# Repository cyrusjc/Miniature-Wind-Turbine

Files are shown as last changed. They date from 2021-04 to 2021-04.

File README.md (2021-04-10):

# Miniature-Wind-Turbine
ELEC 391 Design Project. Miniature Wind Turbine, hand wound generator, 3D printed turbine blades, with a buck converter for MPPT, uploaded onto a cloud server, built with lego.



fig.1 Windmill in question

For the PCB, Altium designer was used, and ordered off of an online PCB manufacturer in china. Voltmeter uses a voltage follower and Ammeter uses Shunt resistor with a differential amplifier.



fig.2 PCB with Boost Converter using 1 diode and 1 mosfet topology.

For the MPPT algo, we used P&O which is state dependent. checks previous power and duty cycle. the flow chart of the logic is listed below:



The MPPT algo is modeled on matLAB using a special function block:



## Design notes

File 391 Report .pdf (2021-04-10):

### ELEC 391 Engineering Report: Wind Tracking Power Generator

### Submitted by:

Name | Student Number
Berk Calis | 31602155
Bruno Rodriguez | 19024173
Cyrus Cheung | 77080844
Felipe Ballesteros | 10703156

### Submitted for: ELEC 391 On Apr 14th, 2019 Professors: Ignacio Galliano Zurbriggen & Cristian Grecu

Abstract

This term, for our ELEC 391, Design Studio course, we set out to design a wind turbine that will generate power from a box fan provided to us. The requirement is that for our wind turbine is that is must meet dimensional requirement of 50x50x60cm and our boost converter must produce 10V - 15V output. Our goal for this project was to create an efficient turbine made with recycled materials. We settled on using legos for our chassis, since one of our members had previously owned them. We designed our turbine to be a 3-phase PMSG. Our generator will be equipped with a MPPT algorithm that controls duty cycle of our boost converter. With our design, we managed to provide 1.4 W of power with a 100Ω load. Our turbine is able to sense the wind and rotate our generator to track our wind with a 180° arc. To complete our system, we created a website, that has four main features: real-time monitoring, historical visualization, analytic services, and an alert system. With our real time monitoring system, we can see the current output of our generator, the data is stored in the cloud and past data can be retrieved and displayed on our website. We can also use our analytic services to process the data we are outputting. If our turbine is not operating correctly, we have an alert system that sends SMS alerts if the voltage, current, or power is either too high or too low. To ensure we minimize time debugging, we took step by step approach while integrating, so we can easily rule out conflicting modules. In total, we spent $379 of our budget, but we calculated with full efficiency, that our design could be replicated with $163. With our original timeline, roughly kept on schedule, we did however integrated our project later than expected. Finally, we discovered that we did not meet our goal to create an efficient turbine, since commercial turbines produce $1.75/W and our turbine produces $116/W. We did however design our design a very modular website that can be paired with any generator with an microcontroller capable of I2C communication.

### 1. Table of Contents

List of Figures | 3
List of Tables | 3
List of Abbreviations | 4
Introduction | 5
Project Description | 5
Goals | 5
Requirements | 6
Design | 6
Generator | 6
Research | 6
Iteration and test | 8
Re-iteration and Finalization | 9
Power Electronics | 10
Research & Calculation | 10
Testing | 11
Optimizing | 12
Finalizing | 13
Sensing and Modeling | 13
Modeling | 14
Prototyping | 18
Finalizing | 19
Controls | 21
Integration | 22
Submodule Assembly | 22
Validation | 24
Structure Assembly | 24
Testing | 25
Extra Website Service | 26
C7 Monitoring System | 26
Data Recording | 28
Data Collection/Processing | 28
Web Application | 29
Real-time monitoring | 29
Historical Visualization | 29
Analytics Service | 30
Alert Service | 30
Cost Analysis | 30
Timeline | 32
Final Remarks | 33
References | 34
Appendix A : Budget Usage | 35

### List of Figures

Figure1: Equations for Reluctance and Magnetic Flux
Figure 2: Reluctance (A*t/Wb) over Area or length (cm or cm2)
Figure 3: 2-phase Voltage for the first iteration of the PMSG
Figure 4: 9 tooth stator (50 mm diameter) and 12 tooth stator design (80 mm diameter) Figure 5: 2nd PMSG iteration output voltage
Figure 6. Average current in the inductor.
Figure 7. First simulation schematic
Figure 8. Demo-2 PCB Design post-testing.
Figure 9. Voltage vs Current Graph for Optimization.
Figure 10. Final PCB Design
Figure 11. Ammeter and Voltmeter in CIRCUITMAKER2000. Figure 12. Simscape Model of our Boost Converter
Figure 13. Model of our Microcontroller in Simscape
Figure 14. MPPT P&O Algorithm
Figure 15. MPPT tracking maximum voltage given bounds of 10V - 15V Figure 16. Rotary Encoder model, logic 1 defined as a step.
Figure 17. Waveform of Rotation of 15 degrees on our stepper motor. Figure 18. Demo 1 Circuit
Figure 29. PCB schematic in Altium Designer 18
Figure 20. 3382G-1-104G schematic and output voltages.
Figure 21. SMD Rotary potentiometer
Figure 22. Final Demo PCB
Figure 23. Final Structure
Figure 24.Architecture of the cloud
Figure 25: Final Gantt Chart of the overall project Figure 26: Gantt chart for demo 2 of the proposal Figure 27: Gantt Chart for the final demo in our proposal

### List of Tables

Table 1. Specifications of our Sensors Table 2. Data Validation of sensors Table 3. Final design bill of materials

### List of Abbreviations

MPPT | - Maximum Power Point Tracking
P&O | - Perturb and Observe
ADC | - Analog to Digital Converter
PMSG | - Permanent Magnet Synchronous Generator
I2C | - Inter-Integrated Circuit
PCB | - Prototype Circuit Board
O.P | - Operating Point
B.C | - Boost Converter
IC | - Integrated Circuit
MISO | - Master-in Slave-Out
IO | - In out
VM | - Virtual Machine
GCP | - Google Cloud Platform
SMS | - Short Message Service
HTTP | - HyperText Transfer Protocol
IDE | - Integrated Development Environment

### Introduction

This year for ELEC 391, we designed a real small scale wind tracking power generator that can output up to 1.4W. Its design is composed of a custom designed PMSG worked on by Bruno, a custom diode bridge rectifier and boost converter on a PCB by Berk, fully designed Simulink control loops, operations and sensing ICs by Cyrus and a MISO arduino controller implemented with an MPPT algorithm and motor control by Felipe.

Our main goal for our project is to develop a small scale wind turbine that can be monitored in real time with software. With the real time monitoring software, we can ensure that our turbine is working properly, as well as display the history of the power extracted with the generator. We created this turbine to be created as economically and environmentally efficient as possible by clever optimizations on each respective part. The project allowed us to gain a proficiency on many open source software applications (SolidWorks, Altium, Simulink, Arduino IDE) and use them to create what we believe is a very efficient wind tracking power generator.

### Project Description

Our wind turbine consists of a Permanent Magnet Synchronous Generator with 12 stator slots and 10 magnetic poles. The generator sits on a lego chassis which connects to a rectifier and a boost converter circuit controlled by an Arduino to produce 10V to 15V DC output and determines the point of max power. The turbine is equipped to measure generator current, voltage, boost converter output voltage and output power. With a load of 100Ω, we can output 1.4W.

For our ammeter, we used a differential amplifier followed by a voltage divider, and for our voltmeter, we used a voltage divider and a voltage follower. For wind tracking, we designed a PCB to fit a surface mounted rotary potentiometer, one on a free spinning blade to rotate with the wind, and the other mounted on our stepper .motor to provide proportional closed loop feedback.

Our wind tracking fin sits on top of the generator and we mounted our generator on a lego chassis connected which are with lego gears and a lego lazy susan with a PCB potentiometer to allow for feedback. The stepper turns the lego gears based off the wind tracker using proportional control with a total of 180 degrees..

On top of all the descriptions mentioned above, we decided to create a website to include a real time monitoring system to track the performance and health of the turbine. The features of the websites include: real-time monitoring, power history visualization, data analyzer, and a health alert system.

### Goals

For this project, we set out to develop a working prototype of a PMSG wind turbine that can be monitored with real time with software from anywhere in the world. With the real time monitoring software, we can ensure that our turbine is working properly, and as well as display historical data such as monthly or yearly averages. We figured this is important when trying to determine the feasibility of planning a wind energy farm. In order to do that, we want to design our website to be as modular as possible which means the online module could be attached to any microcontroller that can interface with our arduino via I2C and we can display the data for that specific generator live in the cloud.

With our prototype, we can determine the feasibility of a renewable source of energy that is portable and can be placed in areas with no traditional power grid. Our main design goal is that we want this turbine to be created as economically and environmentally efficient as possible. This means using recycled parts, or parts we have in excess and trying to minimize our budget. We understand that this means the power electronics will not perfectly optimized and precise, but at the same time we do not require precision as what's important in a wind farm is the monthly power average.

As a secondary goal, we hope to achieve expertise with certain software design tools that will help us in industry later in our lives (ie. Use of SolidWorks, Arduino IDE, Altium PCB, Simulink, etc). Moreover, we hope to gain a level of familiarity with certain tools and machines whilst practicing their respective safety standards at all times.

### Requirements

According to the specifications given, the following are the minimum required parameters for our generator:
1) It has to be a PMSG design
2) MPPT control
3) Wind Tracking
4) DC-DC Boost Converter from 10 - 15V
5) 50 x 50 x 60cm (W X L X H)

For our economical requirement, we were given a budget of $1000, with our grade dependent on our actual spending. In addition to our minimum requirement, we need a monitoring system that can show our output voltage, current, and power.

### Design

For this section, we will split our design process into 5 parts, one for each of our respective roles in our group, as well as integration design.

Generator
The role of the generator design entails the following requirements.
1. PMSG design
2. 6V peak output voltage.
3. Sufficient output current to turn on MOSFET in boost converter circuit

For the design of the generator, we took 3 steps to achieve the requirements: research, iteration and test, and reiteration.

Research
Upon initial research of a basic PMSG design, we found that the main constraint is to have an even number of magnetic poles in order to be considered permanent magnet synchronous. The design of most wind turbines use around 6, 8, 10 or 12 magnetic poles depending on the size of the generator. Since all of these numbers are arbitrary and dependent on how much flux you can extrapolate from each magnet to one of the induced stator coils, there is no real effect on what we choose. In addition wind turbine technology tends to be fairly large but due to the constraints of a 50x50x60 cm dimension boundary for the project, the generator design needs to be fairly small but efficient.

Before we started the design process, we analyzed two sets of equations which determined a baseline for the generator’s parameters described in Figure 1:

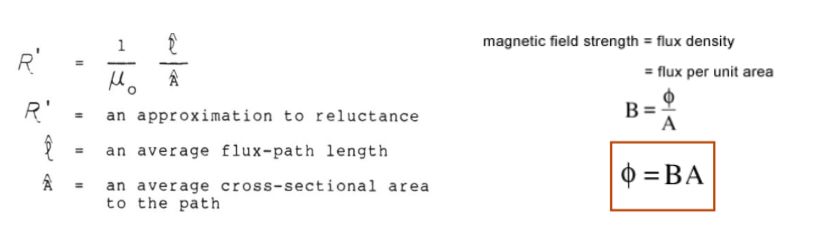
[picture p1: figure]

Figure1: Equations for Reluctance and Magnetic Flux

To generate the most peak voltage at the output we had to analyze the magnetic circuit of the flux being induced for different reluctances. The main factors to deal with the minimization of reluctance was the length of the path and the area of the cross section of the stator tooth. Increasing cross sectional stator area would ultimately lead to higher induced voltage for bigger applications (ie. an actual size wind turbine), however decreasing the size of the path that the flux goes through has a similar effect and would be a more suitable model for cost efficiency for smaller applications such as this project. A graph of reluctance minimization depending on area and length is provided below.

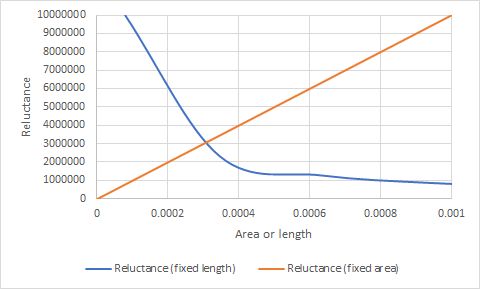
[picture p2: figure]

Figure 2: Reluctance (A*t/Wb) over Area or length (cm or cm² )

In order to achieve a perfect reluctance minimization between an increase in area or decrease in length, the length of the path would have to be less than 0.0003m or 0.3 mm which is too small for a generator. In order to compensate for this, multiple stator teeth would be added for increased surface area and flux in addition to creating a relatively small and compact design in terms of path length to reduce the reluctance.

In terms of voltage and current generation, the amount of turns and gauge of wire plays a big factor. Higher gauge wire meant more turns could be added per stator tooth which leads to more voltage generation however it means that there would be less current due to the resistivity of the thinner wire and vice versa.

Iteration and test
Our first iteration of the PMSG design used 4 magnetic poles on the rotor and 6 stator teeth with around 150 turns per phase and 28 AWG wire. The generator is connected as a wye for simplicity of design. The stator casing was relatively small with a 5cm diameter, 4.5cm height and a cross-sectional area of 7.875 cm²
. This design, although functional, did not meet any real current or voltage requirements as it was 3D printed. Figure 3 shows the simulations of the voltage of the first design in the oscilloscope.

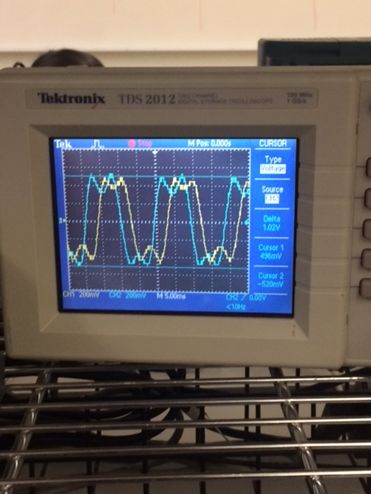
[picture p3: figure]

Figure 3: 2-phase Voltage for the first iteration of the PMSG

The harmonics appearing on the first simulation are a result of a mismatch in terms of reluctance which are due to but not limited to: mismatch in stator tooth area, mismatch in wire inductance, etc.

After testing 25 additional turns per phase (which was the most we could fit in the stator teeth for the current iteration), voltage increased by 0.2V at the output but resistance of each phase also increased which minimized the current output. After testing that design, 2 more designs were made in an attempt to increase the number of turns and magnetic flux.

Re-iteration and Finalization
After testing the initial design and knowing certain constraints about increasing the area of the stator cross-section and length of the stator, we ultimately decided on a slightly larger design with 12 stator teeth to increase the number of turns that could be added per phase. In addition to stator changes, the rotor was changed from a 4 pole to a 10 pole design which increases the effectiveness of each magnetic pole to each stator winding. Since there were more stator teeth, the effective area for magnetic flux increased and more turns with thicker wire were able to be added.

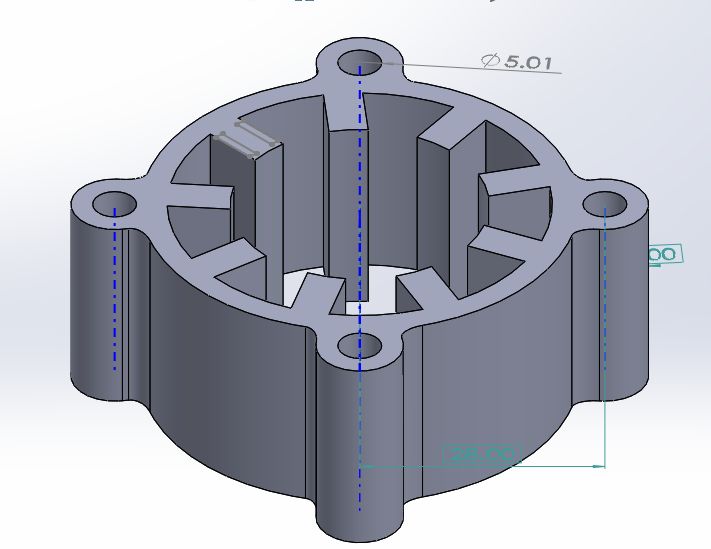
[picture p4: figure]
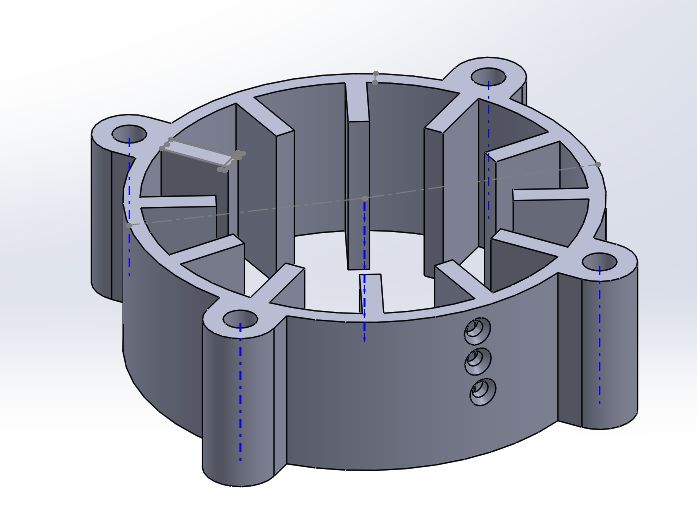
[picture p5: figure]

Figure 4: 9 tooth stator (50 mm diameter) and 12 tooth stator design (80 mm diameter)

For this new design, 300 turns were used per phase at 26 AWG wire to increase the induced current. Again the generator is a wye connected formation for simplicity. This version of the design is able to generate up to 3V peak with just a 3D printed design. Figure 4 shows the 12-slot stator/10 pole rotor’s line-line voltage with the fan.

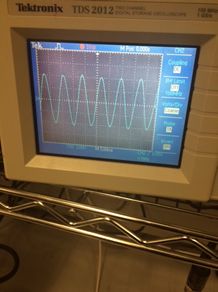
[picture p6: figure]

Figure 5: 2nd PMSG iteration output voltage

Since the permeability of the 3D printed design was just the permeability of free space which is 4π*10

-7
, the voltage and current were still relatively low outputs. However an increase of 50% was expected after water jetting an iron core for the stator which would increase the permeability which will reduce reluctance.

After waterjet cutting the stator and rewinding the 300 turns/phase, the output voltage of the PMSG with the blades and fan (saving talking about fan design for integration area of report) was around 7.02V peak with an output short circuit current of around 0.5 A. This finalized the development of the PMSG as it meets all the requirements for the project. Figure 5 shows the final version the PMSG.

Power Electronics
The role of power electronics expand on the following:
1. Converting AC Voltage from the generator to DC by implementing a diode bridge rectifier.
2. Boosting the converted DC voltage up to 10-15V level.
3. Optimizing power generating so that the chosen circuit components generate the maximum power output when integrated.

For our power electronics design process, we had 3 stages to complete: research and calculation, testing, optimizing, and finalizing.

Research & Calculation

With the research and calculation stage of our design, there were 3 main areas of focus: rectified voltage, current in the inductor and component choices. Rectified voltage is important because we wanted to maximize the AC/DC converted voltage output. To maximize DC voltage, we had to use diodes that had lowest possible forward voltage values while still being able to handle nominal current and power ratings. For this reason, we decided to use Schottky Diodes in our diode bridge and boost converter designs. The current in the inductor was also essential for our design because it is equal to the input current of the boost converter, thus directly influencing the integration of power electronics and generator. Lastly, component choices were integral for our design specifications because of their direct effect on the output voltage, output current, therefore changing the output power. Taking the design specifications into account, we came up with our component choices with the following calculations:

## V in = 6V V out = 12V Duty Cycle = (1 − V

V
o

in
ut

) = 50%

## Δ Il = 10% Δ vo = 3.75% fsw = 10 kHz Rload = 80 Ω

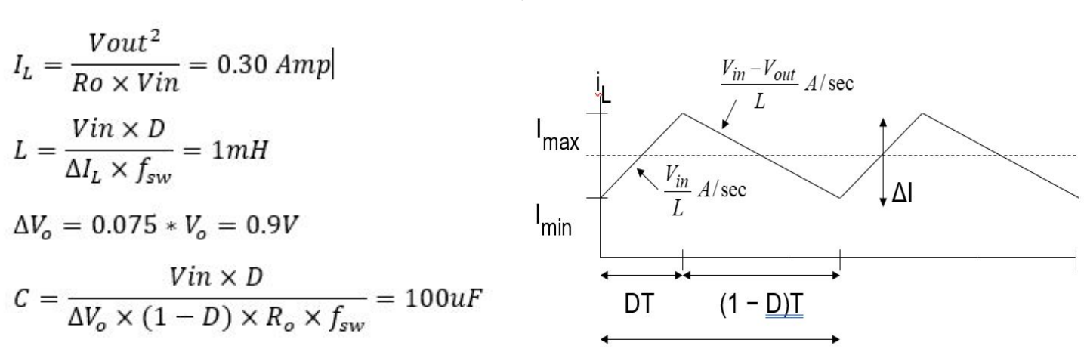
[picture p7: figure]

Figure 6. Average current in the inductor.

Testing
After deciding on the components for the design, we started simulating the design that we came up with, so that we could see if it would work if we were to implement it on a breadboard.

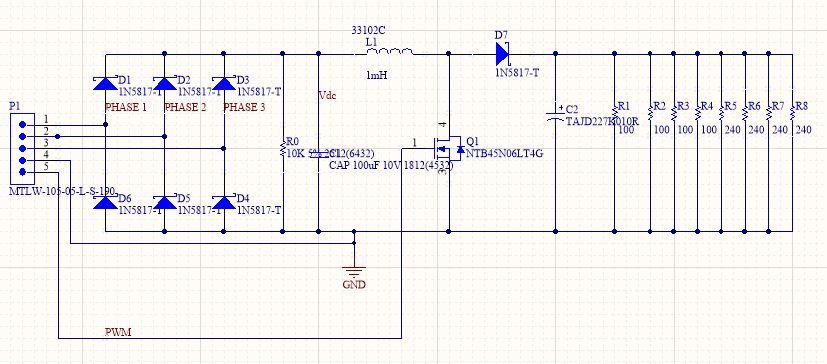
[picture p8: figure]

Figure 7. First simulation schematic

After seeing our simulation is working, we decided to try it on a breadboard to begin with. We divided our implementation into two parts: Diode bridge and boost converter. To avoid unnecessary reiterations, we emphasized on a step-by-step principle that allowed us to be on point when we were dealing with bugs or mistakes. Thus, we initially started the implementation of the diode bridge with a single phase full wave rectifier using 4 diodes. Once we made sure the rectification is how we want it to be, we wired up the circuit into a

3-phase diode half-bridge. For the 3-phase source, we used the test generator that came with the project kit. Just as our simulation showed, the diode bridge was working as it should be. We then move on to the harder part, the boost converter. For this part, the initials tests were conveyed by the use of the DC Voltage Supply as the Vin, and the Function Generator acting as the PWM at 10kHz and 5V which was connected at the gate of the fast switching power mosfet of our circuit. During the testing of boost converter, we realized that the calculated capacitor value of 100uF was not enough to filter the ripple, therefore we increased the capacitance to 220uF for the boost converter filtering even it it meant bigger voltage discharge and possibly higher current spikes. Although we made the boost converter work, the circuit needed 0.3 A to operate, which was a lot of current to expect from the generator. To make sure that it would not cause a problem for us during integration we increased the output load to 220 ohms so that the current requirement for the integration would drastically decrease.

Figure 8. Demo-2 PCB Design post-testing.

Optimizing
After integrating both parts, we realized that the power output is not at a level that we desired it to be. Test generator was only operating at 0.04 Amps, and to provide that we had to use a load bigger than 220 Ohms. Before changing anything, we wanted to see how much current our generator could provide so that we could optimize the load for the best output power. The generator that we build was able to provide us more than 0.2 Amps, therefore we began our optimization. After trying many load resistances and logging them, we found the optimal value for the load resistor which gave us the maximum power output at 50% duty cycle.

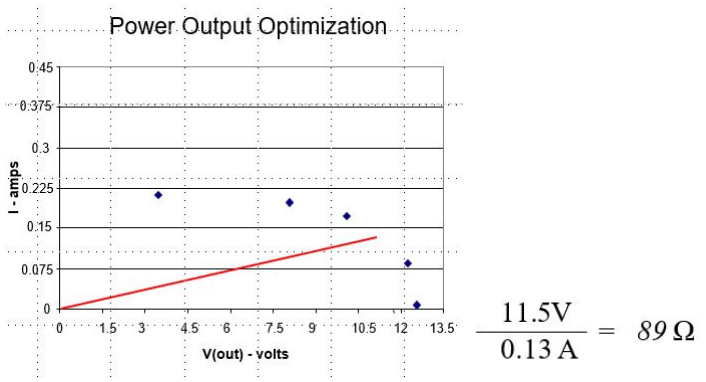
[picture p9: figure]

Figure 9. Voltage vs Current Graph for Optimization.

Using 89 ohms was supposed to give 1.49 Watts power output for our design:however, we decided to go with a resistor we had an easier access for: 100 Ohms. With a 100 Ohms resistor, our output power was still very close to the maximum and it would also operate under a lower current, which would both make our design safer, and our voltage output higher. The output of our final design was 1.40 Watts.

Finalizing
With the optimization done, we went on to finalizing our design’s power electronics part on a PCB. We did not want to have multiple PCBs due to the space they occupy in our structure and their high cost of manufacture. For this reason, we integrated the power electronics and the sensing together into a single compact PCB which saved us money and space. Here is the final design:

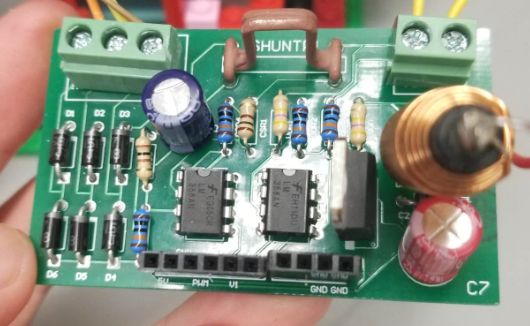
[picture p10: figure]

Figure 10. Final PCB Design

Sensing and Modeling
The role of sensing and modeling entails the following:
4. Voltage, Current sensing

5. Wind angle position, generator angle position
6. MPPT Models and sensor models

For our sensors’ design process, we took four steps from inception to completion: research, modeling, prototyping, and finalizing.

Research

With the research stage of our design, we found that there were 2 main implementation of the current sensing: the hall effect sensor, and the shunt resistor. The hall effect sensor takes into effect the magnetic field produced with a current in a wire to produce an analog signal, while the shunt resistor produces a voltage drop across which is what is measured. We decided to go into with the shunt resistor due to its popularity and ease of implementation on a prototyping board. Initially we used a 0.01 mΩ, 2 terminal resistor, but after speaking with the TA, we discovered about 4 terminal resistor, which gives much more accurate readings. However a 4 terminal resistor is very hard to use while prototyping because they don’t fit in traditional breadboards or perfboards. We decided to prototype the 2 terminal resistor but implement the four terminal resistor on a PCB. In addition we want to decide minimal power loss, so we wanted a small shunt resistor, but due the small voltage drop in a shunt resistor we need to amplify the signal. We decided on using a differential amplifier with a large gain to amplify the small signal. We used a voltage follower after the differential amplifier to isolate the circuit.

For our voltage sensors, there are not that many clever ways of achieving this, so we went with the simple voltage divider. We also used a voltage follower to isolate the circuit. A very important safety design we came up with was to supply the op-amps with 5V. With a 5V supply rail, if our generator output a much higher voltage such that the divider exceeded 5V, it would saturate, and the microcontroller would be safe. The equations for our voltage divider and differential amplifier is as follows:
V out = V in | & R2
R1+R2 | V out = (V 2 − V 1) R1 R2

For our wind sensors and generator angle sensor, there were two main ways we could implement it with, the rotary encoder, and a rotary potentiometer. Initially we used a rotary encoder that pulses a logic 1 when the encoder rotates by 15 degrees. But we discussed that it would be difficult to implement this with feedback control, so we decided to use two identical potentiometers with their initial angle oriented in the exact same manner, that way we can compare their analog values to determine whether or not they are aligned. We decided to go with SMD rotary encoders as they are cheap, low friction, and can sit flat nicely on our legos.

Modeling
Following the research stage, we modeled our sensors and MPPT using CIRCUITMAKER2000 (SPICE) and simscape. To ensure that our sensors would work we modeled them in circuit maker as shown below in figure 11.

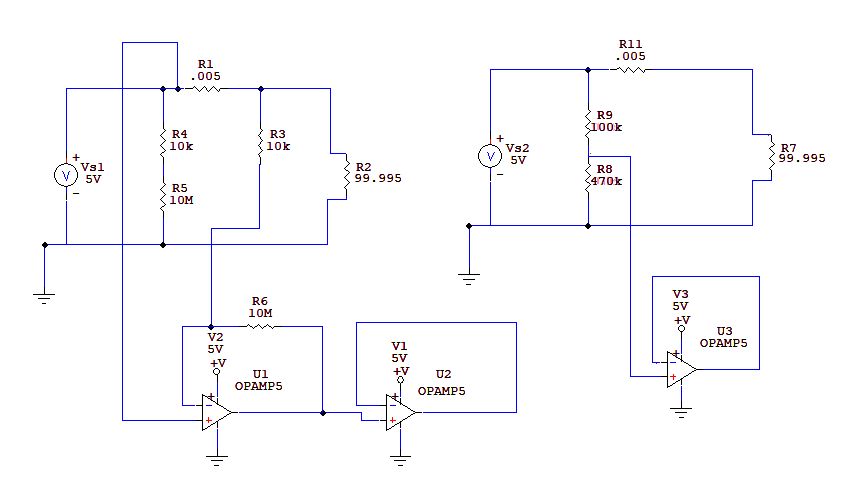
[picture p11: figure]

Figure 11. Ammeter and Voltmeter in CIRCUITMAKER2000.

We simulated this circuit with the DC O.P and found that values were exactly what we expected. We could then push this into prototyping.
For the boost converter and MPPT, we modeled our system using energy flow modeling (physical modeling) as shown below. We tried to model our system as close as possible to our real system, that is we added the voltage divider resistors and the shunt resistor.

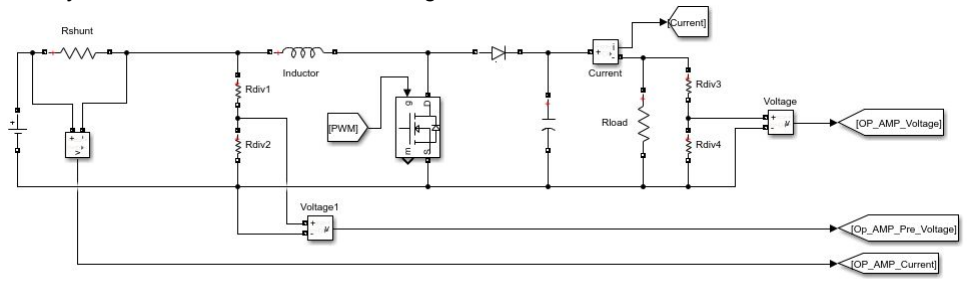
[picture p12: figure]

Figure 12. Simscape Model of our Boost Converter

To further simulate our real system we modeled the microcontroller. Every step that the microcontroller takes to convert our ammeter signals and voltmeter signals is taken to ensure that we can easily go from our model to our real system. For example, from the voltage divider, our microcontroller ADC takes in value that range from 0 to 1024 (10-bit). We modeled that and to convert from the voltage at our boost converter, we simply divide by 1024, and multiply by our voltage divider value which is 3 in this case.

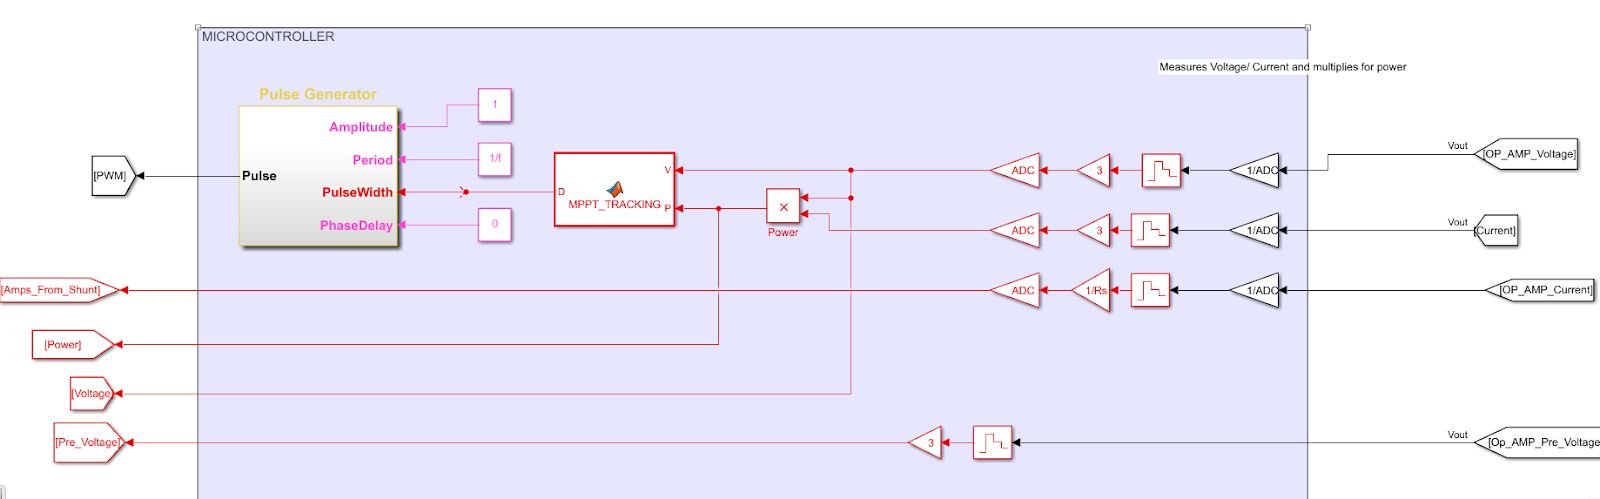
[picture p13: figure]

Figure 13. Model of our Microcontroller in Simscape

For the MPPT, we have chosen to use the perturb and observe algorithm. Upon researching MPPT algorithms, the P&O utilizes sensors we already have, thus is the cheapest to implement. Other algorithm require additional sensors, and will be more expensive to implement which oppose our design goal. The main drawback to using P&O is that the it the slowest algorithm. However this is not important to us as we feel that a difference of a few seconds is irrelevant since a wind turbine’s most important parameter is it’s monthly output power. With that reason we believe that it’s not worth it to implement additional sensors to speed up our MPPT algorithm. For our MPPT modeling, we used a MATLAB function block. This block takes in the voltage from our boost converter and the power of our generator, and outputs a PWM. We coded this MATLAB block using the the MATLAB scripting language. This language is very similar to C code and can be easily implemented with minimal changes. Our code is shown below in figure 14. The advantage of using this type of modeling is that it is purely mechanical when converting from our simulated models to our real life system. It is very easy for anyone interpret and implement our sensors and our MPPT algorithm based off our model. One would only need to change the duty cycle implement, sample rate, and starting duty cycle. Our MPPT is shown working below in figure
16. Since we used a voltage source, we can see that the voltage is limited to 15V as specified in requirement. The limitation here is that since we are using an ideal battery source model in lieu of our generator model, the source can provide unlimited current which puts our power to unlimited if no bounds are specified. In reality, our generator will only output a finite amount of current, which will limit our MPPT to between 10V to 15V. In order to complete this model we require a exact working model of our generator, which we could not complete given the time frame.

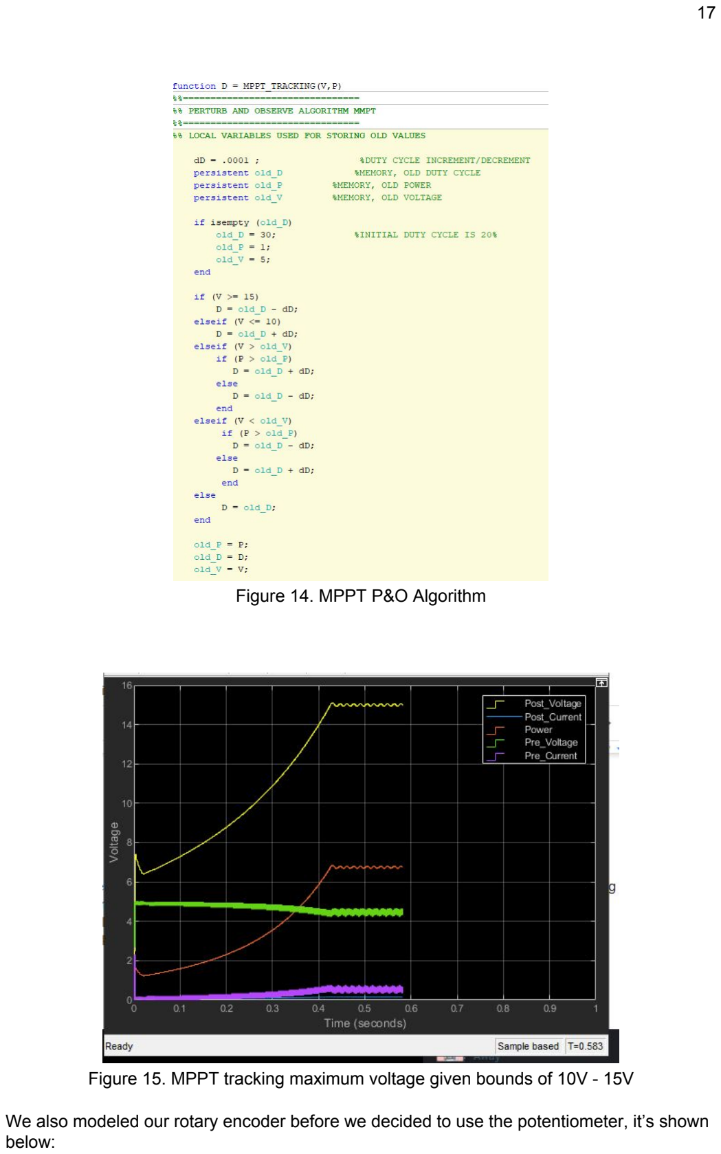
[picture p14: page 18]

Figure 14. MPPT P&O Algorithm

Figure 15. MPPT tracking maximum voltage given bounds of 10V - 15V

We also modeled our rotary encoder before we decided to use the potentiometer, it’s shown below:

Figure 16. Rotary Encoder model, logic 1 defined as a step.

This model was created before our idea of using two potentiometers. Our model takes a unit step from our encoder pulse, and rotates the generator by 0.3 rads ( 15 degrees) as shown on Figure 18:

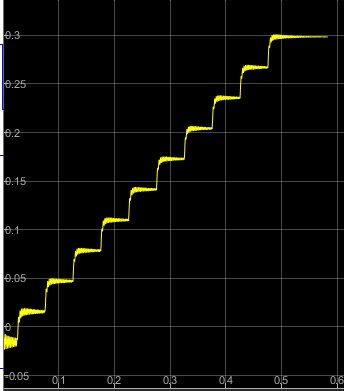
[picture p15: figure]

Figure 17. Waveform of Rotation of 15 degrees on our stepper motor.

Prototyping
With our modeling done, we can move on to prototyping. First we needed to select our op-amps. We wanted our microcontroller to power our op-amps as a safety measure just incase the voltage ever got too high. So we decided to use a single rail supply op-amp. Since we purchased elec kits from previous years, we had plenty of spare op-amps that were not used. In spirit of recycling we decided to use the LM358AN. First prototype was successful as shown in demo 1. As a reminder this is what our demo 1 circuit was, it’s shown on the below in figure 19. In this prototype the 2 terminal resistor was used as mentioned above, it is a 0.01 Ω resistor coupled with a differential amplifier with a gain of 100. We used a voltage divider of 1/3rd (R1=100kΩ and R2=200kΩ) for our voltage divider. This circuit worked perfectly for demo 1. Since demo 1 is a proof of concept, we didn’t exactly plan out what our nominal current and voltage would be so the prototype ammeter was rated for low currents, and the voltmeter went up to 15V as specified in the requirements.

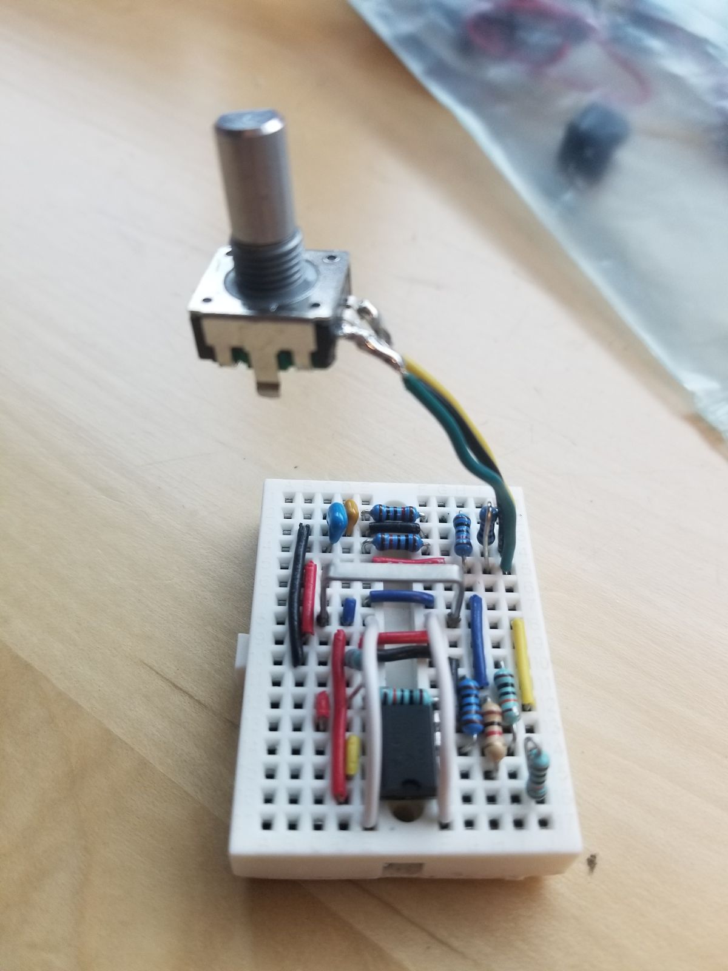
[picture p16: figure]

Figure 18. Demo 1 Circuit

Finalizing
With our prototyping finished, we went on to finalizing our design on a PCB. We drafting up a PCB design using Altium Designer and our design is shown in figure 19 below.

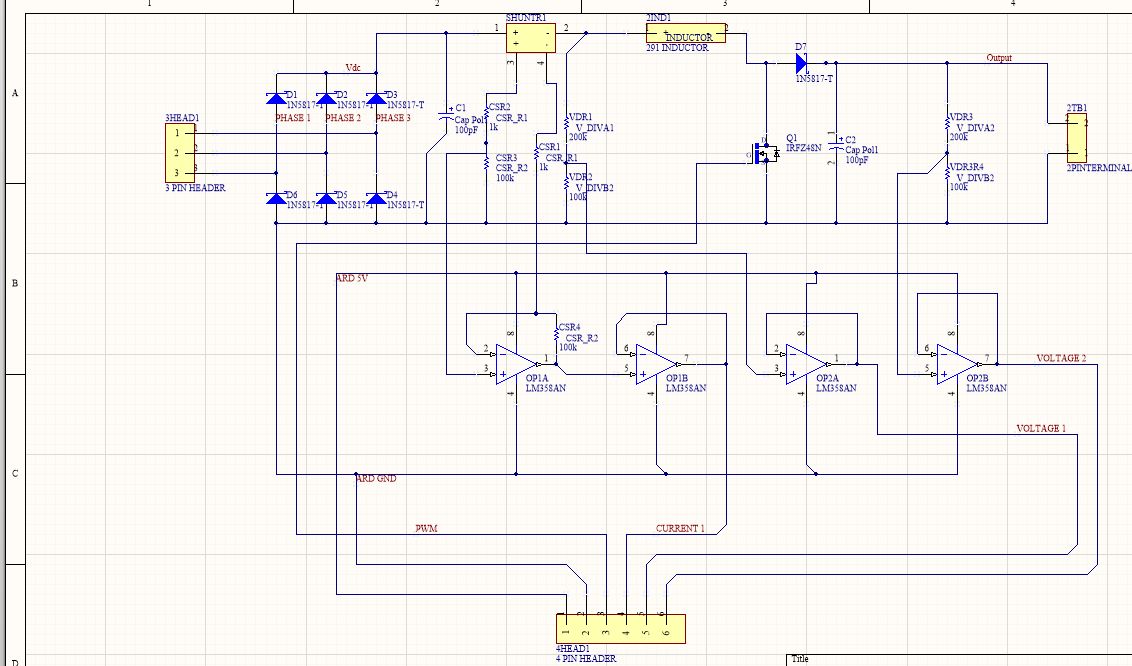
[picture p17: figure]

Figure 20. PCB schematic in Altium Designer 19

And the final PCB from that schematic is shown under the integration section at figure 23 page 24. In this PCB, we replaced our 2 terminal shunt resistor with a 0.005Ω 4 terminal shunt resistor. At this stage of the design we had a clear idea of what the output current of our generator was, so that we could design around it. We decided to set a nominal current of 1A. At 1A, we get a voltage drop, 0.005V, and we want to amplify it such that it’s sufficient to read. We decided to use a gain of 1000 ( R2 = 100kΩ , R1 = 100Ω), such that at nominal current we get a reading of 5V for our microcontroller. Realistically, our turbine only generated 1A but we wanted create our PCB so that it was modular and compatible with other generators. This means over-specifying our sensors such that they can be used on any generator that can supply up to 1A. For our final design, we also recalculated our voltage divider values. We found that when we approached 15V with the old setup, voltage output of our voltage follower were not accurate. We did some research and found that when the op amp is close to saturation and output is close to the supply voltage ( 0V or 5V), we get inaccurate readings. To remedy this we dropped our voltage even further with a ratio of R1

/R2 of 4.7 ( R1 = 100k, R2 = 470k). This dropped our voltage from 1/3 to 1/5.7. This gave us more accurate readings when we approached 15V. With this setup we can plot the specifications of our sensors in table 1 below. We assume the generator will operate at a nominal values of 5V at 1A, and that the post boost is 15V.

| Max before damage | Max before saturation | Min | Resolution | Power loss
Pre Boost Voltage | 50V | 28.5 | 0 | +/- 30mV | 43uW
Post Boost Voltage | 50V | 28.5 | 0 | +/- 30mV | 390uW
Current | 23A | 1A | 0 | +/- 5uA | 5mW
Table 1. Specifications of our Sensors

And thus, our sensors meet the required specifications listed in the requirements section. The validation of our current and voltage sensors will be discussed below.

For our wind sensors, as discussed above we decided to go with a rotary potentiometer instead of a rotary encoder. We purchased a low friction SMD rotary encoder (3382G-1-104G). We picked this sensor because it provided us with a linear relationship, and it was small and portable such that it could be mounted anywhere.

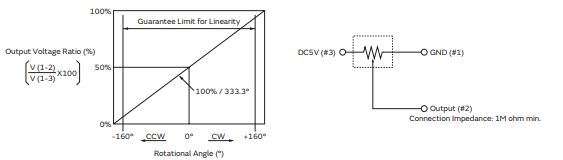
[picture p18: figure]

Figure 20. 3382G-1-104G schematic and output voltages.
https://www.murata.com/~/media/webrenewal/support/library/catalog/products/sensor/rotaryposition/r51e.ashx

The only drawback was that we had to design a PCB for it. Luckily for us, with the tutorial directed to us by Professor Nacho and Professor Grecku, we had the knowledge to design the PCB which makes this trivial. The SMD component required a simple schematic which is shown in the data sheet which we’ve pulled and displayed in figure 21. Since the schematic is very simple, it’s very easy to implement the PCB for the SMD potentiometer.

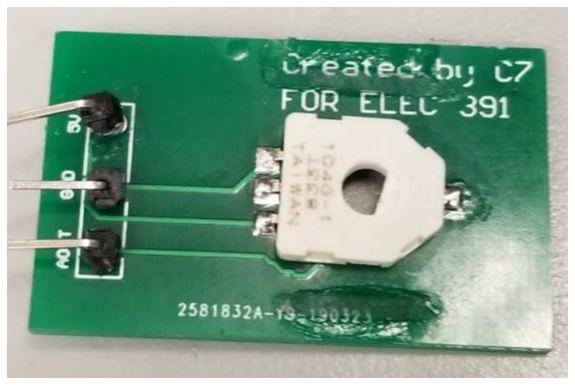
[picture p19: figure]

Figure 21. SMD Rotary potentiometer

Controls
The controls systems was built using one single Arduino Uno and it was flashed using the official arduino IDE. The following are tasks assigned to the control:
- Generate PWM
We had to provide a PWM with variable duty cycle to the boost converter in order to be able to function properly. The PWM was generated by using one of the 3 timer registers of the Arduino Uno, to be more specific, it was implemented using Timer_1 configured to run at Fast PWM mode.

Timer_1 was configured by writing to the internal registers of the arduino by referring to them using globals variable provided by the arduino framework bindings/mappings. The configurations for each individual register used to control Timer_1 where taken from the official Atmega328P data sheet, as well as from various open source references and frameworks.

- Read Analog data from sensors
The sensing of our turbine’s parameters was done using analog sensors which are fed into the arduino’s internal ADC. In order to read and process this data, a open source State Machine design pattern framework called Automaton was used. Automaton framework lets you create state machines that react to stream of events and (inputs) and transitions between states performing actions on each state. Automato_Analog machine is a timer based machine that reads values from an analog pin from the arduino and the triggers callback to use the data in the main process. The callback frequency can be updated and the data of the analog pin can be averaged automatically while the machine idles waiting for the callback to send the average as one of the callback parameters if desired.
A total of 5 automaton machines were used, one for the pre boost voltage sensor, preboost voltage sensor, current sensor, wind direction sensor, and wind turbine position sensor. Each sensor was configured differently and data was averaged and process differently in each callback.

- MPP Tracking
MPPT tracking was developed by using a P&O algorithm in which the current power and voltage is compared to the previously read power and voltage, the duty cycle is then changed. 1.5 seconds are allowed for the system to react to the duty cycle change before the algorithm is called again and the process is repeated every 1.5 seconds. The MPPT is triggered by the same timer that calls the wind position function, when ever the timer counter hits 1.5 seconds the MPPT is called gain.

### Integration

Submodule Assembly
For our integration concept, we tried our best to modularize individual parts and we parallelized our individual parts to fast-track our project. This allowed us to quickly have every submodule of our project ready for integration. Our integration is centered around having a PCB with ports than can easily be melded together. We created a centralized PCB that could be connected to most of our submodules. All of the ports that connect to the PCB are either terminal blocks or arduino header pins, which allows us to easily connect and modify our submodules if needed. This made integration easier as we could connect and disconnect the the generator, load, and the arduino from this PCB easily. Our PCB is shown in figure 23.

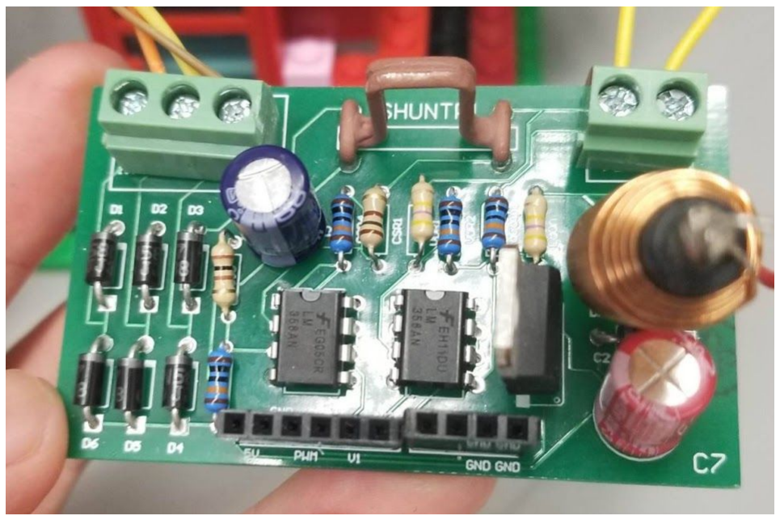
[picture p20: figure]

Figure 22. Final Demo PCB

We can split our integration into 3 steps:
1. Verifying individual components.
2. Integrating sensors with power electronics.
3. Integrating sensors, power electronics, and generator.
4. Integrating sensors and controls.

First of all, to ensure smooth integration, we tested sub modules to verify that it was completely functional before merging our modules sequentially. This allows us to debug easily as we would know which modules are conflicting with each other. This was our task for demo 2.
Secondly, we want to integrate the sensors with the power electronics. As we can see from figure 23, right from the start, the sensors, and the power electronics have already been integrated. We first supplied 5V DC before the shunt resistor, and supplied a pwm of 10kHz with 50% duty cycle. With the oscilloscope, we made sure each measurement made sense before moving forward. For example, we expect 10V post boost converter, then our analog voltage is calculated below. The 5.7 is the ratio of voltage divider as calculated in the sensor design part of the report.
V analog = 5V / 5.7 = 0.877V And our post converter voltage as:
V analog = 10V / 5.7 = 1.754V Once we verify that everything is working, we move on to the next step.

Thirdly, the generator is easily integrated to sensors and power electronics. In our PCB, we have a terminal block so that we can easily in plug our three phase generator and our load. Instead of the 5V DC supply, we attach our generator to the rectifier. With the exact same process as step 2, we test our generator, boost converter, and sensors with the oscilloscope. We expect it to work flawlessly, since the it worked with our 5V DC supply, with the only difference being the generator used as a supply. We clamped the generator down using the vice grips available in the labs. Once we verified that the generator, boost converter, and the sensors are working, we can interface with controls.

Finally, we integrate everything together. To interface our PCB with our micro-controller, we send our analog signal to a arduino compatible header pin. We can use dupont cables to attach these pins to the pins of the arduino for a clean look. The arduino has a 10-bit ADC, which means we have to convert the ADC value into voltage, current. For our voltage sensors, to convert our value we use the following conversion:
V | DC | / ADC value actual | = A | reading

* Rdivider * V Max

V | DC | 5.7 | 5 / 1023 generator | = A | preboost * | *
V | DC | 5.7 | 5 / 1023 boost converter = A | post boost * | *
Similarly, for our current sensors we the following conversion:
I = ADC | V | / (ADC value | )
reading
* max | * Rshunt * GOPAMP
Igen = ADC | 5 / (1023 | 0.005 | 1000)
current * | * | *
The accuracy and verification of our data will be discussed in the data validation section below.

For the potentiometers, we bought a potentiometer with a linear relationship between angle and voltage. We place our two potentiometers with their references identically aligned with 0° facing the front of the generator. We then know the wind direction is changing if we compare the two ADC values. The wind spins the potentiometer which changes the ADC value, which signals our stepper to rotate our generator until the ADC matches. Since we’re using references, no conversions are needed.

With all the parts fully integrated, we can move on to data validation.

Validation
In order to ensure that our sensors are accurate, we had to validate our data to ensure that we are correctly reading output voltages. We created a table to compare our sensor readings with that of a known accurate sensor. In our case we compared our sensors with the oscilloscope. This data is constructed in to table below:

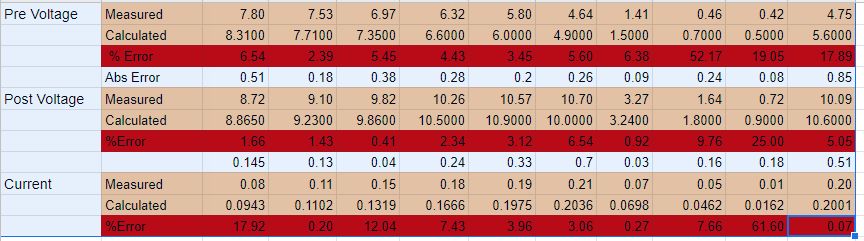
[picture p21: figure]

Table 2. Data Validation of sensors

As stated in the sensors design section, when we reach the upper and lower bound of our sensors (0 and 5V in all cases), we can see that there are huge inaccuracies. Another reason of inaccuracies could be due to the incorrect reading of the oscilloscope. Since MPPT is changing output voltage and input current constantly, we might not be reading the correct values as it’s changing constantly. In our case when we took these readings, we had our MPPT change duty cycle every 0.1s. This can be hard to read as we cannot instantly read a voltage value at a single time instant from the oscilloscope and compare to the voltage of our sensors. To remedy this error, we recalibrated our sensors to be accurate at MPPT O.P, to ensure that the voltage readings are completely accurate at our O.P. The result is that at about 70% duty cycle, we get a voltage error of about .3% and an absolute error of 0.03V ( 12.1V vs 11.8V)

For our rotary potentiometers, we verified they were working by attaching them to the analog pin of our arduino. We see that they exactly match the linear relationship specified by the datasheet.

Structure Assembly
In our design, we chose to use legos to build the structure for 2 main reasons. The first one is the low cost: We had spare parts of legos that were supposed to be recycled if they had not been used for this project. We as a group took our chances and decided to build the entire structure out of legos. The second reason was the flexibility of restructuring. If we were to use any other material or 3D printed parts, we would have to buy or make new parts if we wanted to change something in the design. Meanwhile with legos, we could make any shape we wanted in no time, saving us time and money. Moreover, we used lego glue that we already had to stick the pieces together to increase durability for the vibrations and shaking created by the fast speed turbine.

Our structure is made of various levels that hold a different part of our design on each.At the base, we have the cave-like structure that hosts the 2 Arduinos. On one of the sides, we have the load for the power electronics under a roof. On the levels above the ground, we have the power electronics PCB and the stepper motor respectively. PCB had to be placed not too far from the Arduinos and the load due to their direct connection on terminals. The stepper motor has a semi-long block placed vertically that has another gear on the top and is directly in contact with the gear, which the entire turbine was built. This allows the stepper motor to be able to rotate a very big structure (the turbine) without the need of a big torque. As mentioned earlier, the turbine (generator and the blades attached to it) are placed on the gear on the top. Finally, the wind sensing parts and the PCB that contains the ADC are placed behind the turbine.

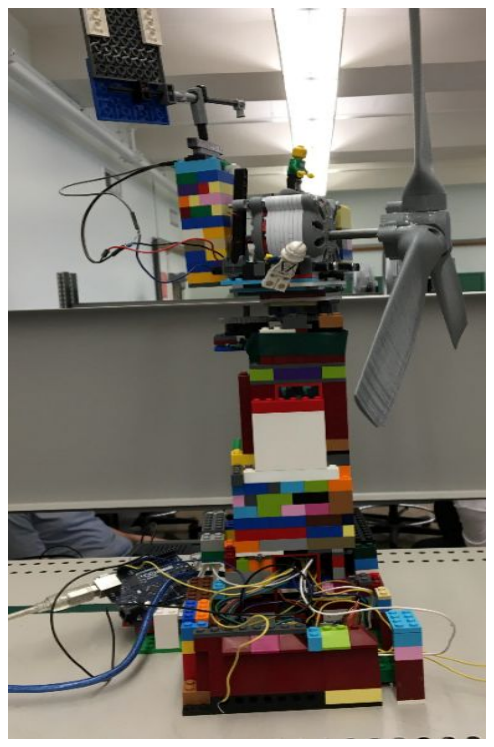
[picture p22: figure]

Figure 23. Final Structure

Testing
With our new chassis we had to verify the integrity of our structure and its ability to withstand our turbine while its operating. Since we created our chassis out of lego, we took necessary precautions by glueing our legos together to try to minimize the vibrational energy. We were pleasantly surprised at how minimal it wobbled under operation as demonstrated in the final demo. We did notice that our structure slid on the metal desk, so we remedied this problem by adding some rubbery electrical tape to increase friction.

We noticed that after integrating everything, that our integration introduced some noise into our system. Our previously clean ADC readings were being polluted by something in our system. To ensure we get steady values, we added some capacitors across our stepper motor, and our sensors. We also performed some software filtering by averaging values. As discussed later, since we settled on a duty cycle increment period of 1.5 seconds, and we’re sampling our ADC every 1ms, we performed a running average of 500 values to smoothen our readings.

We can then test our MPPT algorithm. Implementing our MPPT algorithm seamless. Recall from our modeling that we actually simulated our MPPT algorithm with matlab blocks, which made transplanting our MPPT algorithm to C code very easy. To validate our MPPT, we attached a 100Ω as our load for our generator. Then to find the duty cycle corresponding with maximum power, we manually changed the duty cycle to determine where our MPPT duty cycle was. We found that it was at 70% was where the we got the highest power. After knowing the MPPT duty cycle, we initialized our MPPT algorithm. To verify that the algorithm works, our algorithm would keep the duty cycle to 70%. Initially we changed our duty cycle every 100 milliseconds and increment it by .1%. We noticed that this was not optimal as the inductors and our capacitors had no time to settle. This led us to increase our duty cycle increment, and the period at which we incremented our duty cycle. We finally settled on a duty cycle increment of 1%, with a 1.5 second period.

When testing our wind tracking close controlled loop, we noticed the wind fin does not correctly align with with the wind direction of the fan. We narrowed the problem down to the the single sided wall that is on our benches. It seemed that wind was being reflected off the walls and pushing our sensors towards one direction. Luckily for us this was an easy fix as it was a constant offset from the centre. We corrected this within the code.

Once we tested that everything was indeed working, we could upload our data to the cloud and onto our website.This website and it’s construction and feature will be discussed the in the following section.

### Extra Website Service

C7 Monitoring System
We decided to include a real time monitoring system to track the performance and health of the turbine. We believe that this is a vital feature that every turbine should have, thus the system was built using a modular design pattern; which means, that our monitoring system should be able connect to any other turbine control system in a seemingless fashion.

The website is till live and can be viewed at: https://monitor.febgdev.com. How ever, because having cloud services running costs money, the website is static, meaning that data is currently preloaded and the web app will NOT connect to the cloud services. Please contact any of the team members if it is required to deploy the services again for demonstration purposes.

In order to be able to explain this section in detail it is important to first define the following terms since they are going to be referenced in the next sections.

- Microservice Architecture: Architectural style in which a collection of small independant services (server <-> database pair) is used instead of a single big monolith service.

- Microservice: Independently runed, deployed and maintained server <-> data base pair. One of the services of a microservice architecture collection
- Docker Container: Portable lightweight isolated OS environment (similar to a VM)
- EC2 Instance: Amazon Web Services linux server (linux machine running on cloud)
- noSQL database: Database which stores Object data types instead of SQL type columns and rows in a table

We’ve also constraint our website to the following requirements:

- Secure Connection (SSL)
- Certified Domain
- Built using microservices
- Run on docker containers (Lightweight VM’s)
- Hosted in the “Cloud”
- Accessible from anywhere in the world
- Use noSQL databases
- Handle at least 100,000 Req/sec
- Auto Scalable
- Stream live data (Less than 500 millisec latency)

In order to be able to accomplish all of our requirements we decided to create a web based service “C7 Cloud Monitoring” to which anybody could access by using a web browser. The information being monitored on the web application is polled from any microcontroller attached to the turbine (provided wifi/ethernet capabilities). This information will be then be processed and stored safely in a cloud database. C7 Cloud Monitoring resides on top of a combined stack of cloud services powered by Google Cloud Platform and Amazon Web Services. The specific technologies and architecture used for this feature will be explained below in detail. Below, a flowchart of the cloud services network created for this project.

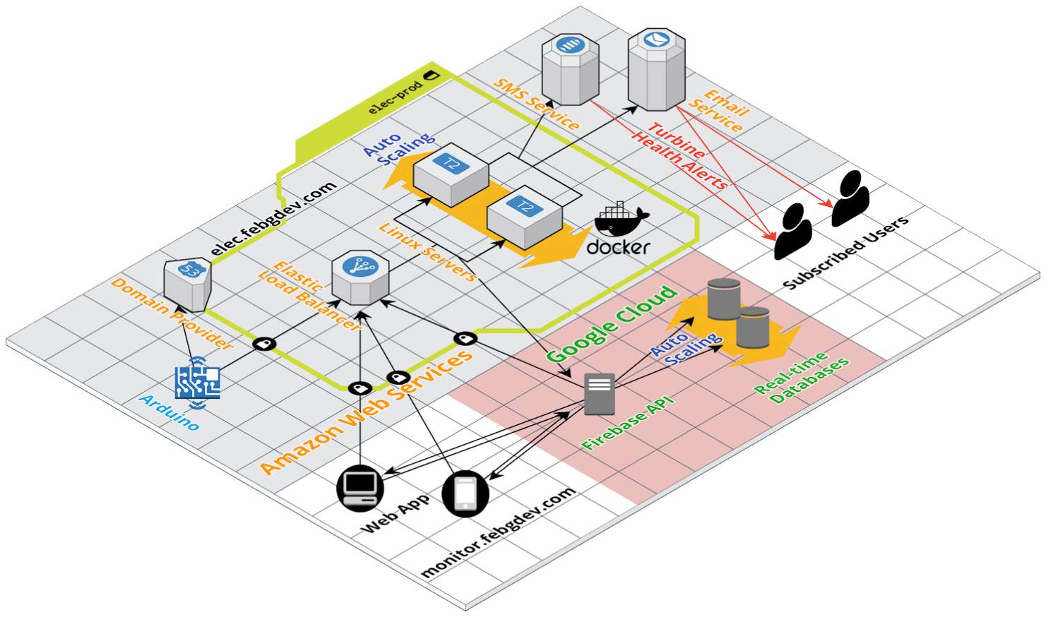
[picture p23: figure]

Figure 24.Architecture of the cloud

Data Recording
As mentioned in previous sections, the main functionality of the turbine’s control is to record information about wind, duty cycle, pre/post boost voltage and current in a periodical basis to be used for orientation and MPPT. In order to be able to upload data to cloud in a seemingless way, the control’s main logic is simply extended by taking the already recorded data and transfer it an Arduino WIFI (slave) over I2C protocol every second. The slave Arduino WIFI establishes an HTTP connection with our dedicated data collection server which will process and store the data.

By using this approach we are able to meet an important aspect of the “Add-on” requirement. Our arduino slave could be attached to any other microcontroller supporting I2C serial communication through two pins (SDA, SLK). This would enable them to upload data to the cloud by simply “printing” to the connection.

Note that this is not necessary if the microcontroller supports wifi (Eg. Raspberry pie) or if it uses an external wifi chip (Eg. ESP8266). In this case data can be sent directly to our cloud server over HTTP request by one simple call.

Data Collection/Processing
Our first microservice is Node.js server built on top of the well known Express framework. This service exposes and HTTP REST-API to which the arduino and other services can communicate. In order to host this server on the cloud, we decided to use and configure an AWS EC2 instance which is nothing more than a custom made linux machine running on our own cloud network.

This server is used as a gateway between the arduino and the database, it takes the data being passed by the arduino and then it securely encrypts and redirects the data to a real-time database. It is also used as the gateway through which any engineer can instantly access to information about the turbine as well as logs from the microcontrollers without the use of the web application (Debugging, maintenance, etc).

Lastly, since this is the service that process and stores data this is the service responsible for handling at least 100,000 Req/sec mentioned in the requirements. This requirement was chosen with the idea of ideally having not one but many turbines in a wind farm. So for example if we have a wind farm with many turbines all sending data multiple times per second we need be able to handle and store all of those requests. This was accomplished by configuring and deploying an Elastic Load Balancer on AWS. The load balancer is configured to receive all the requests and then route each request to different identical copies of the same Node.js server that was mentioned above. So for instance, suppose we have 10 turbines sending data at exactly at the same time, without a load balancer a single server had to handle all 10 request at the same time. Now if a load balancer is attached along with one more identical copy of the server, the traffic is distributed evenly between the two servers, so they both handle 5. In order to avoid wasting resources when not being used (Eg. having two servers when we only have 1 turbine) custom scripts were written to configure auto scalability for the load balancer. This means that the load balancer will analyze the traffic that it is receiving, and decide based in out configuration how many server are needed to server that given traffic. If the actual server count is above the calculation, then the load balancer kills a server, if the calculation is below then it simply deploys a new copy.

Normally instantiating a brand new linux machine with a custom Node.js server take quite some time. For this reason our Node.js server runs inside a docker container as specified by our requirements. Docker container can be booted from zero-to-online in less than a minute. This helps with the efficiency of our load balancing by killing and booting machines faster.

Web Application
We created 4 core services for our website: real-time monitoring, historical visualization, analytics, and an alert service.

Real-time monitoring
Our real-time monitoring feature streams live data from the wind turbine. This service was built using Firebase and it is hosted in Google Cloud Platform. The firebase server was written in Node.js and was able to connect via WebSockets to the same real-time database used by our data collection service. This service was chosen to be served in GCP because the real-time database is also hosted in GCP, thus there is less latency in the connection between them.

Historical Visualization
This feature is hosted in the same firebase server as the real-time monitoring system in GCP. The differences is that is its an static RESTful-API that GETS a single query from database. For this service, the user is presented with a calendar in the web app. The user con pick a range of dates with time with a precision of up to 1 second (Eg. April 1st, 2019 -10:49:25 am). The web application sends this parameters to the GET end point and the server returns all the available turbine data for that range of dates. The data is then presented to the user in the from of line charts.

Analytics Service
This feature is hosted in the same RESTful-API than the Historical Visualization service and it accessible through a different HTTP end-point. Like for the Historical Visualization endpoint, a range of dates is passed to the server as parameter of an HTTP GET request. The server then uses this parameters to fetch all the data available in between those dates. In contrast to the Historical Visualization, this time data is not just simply returned to the web app, inteads the server process the data and calculates the following data:
- Average voltage, current, power, duty cycle throughout the entire range
- Average voltage, current, poser, duty cycle per DAY throughout the entire range
- Average voltage, current, poser, duty cycle per HOUR throughout the entire range

The data is then sent back to the web application, and it is presented in the form of pie graphs and bar graphs.

Note 1: Any other desired type of analytics algorithm can be easily added to the service in the from of Javascript scripts.

Note 2: Average voltage, current, poser, duty cycle per HOUR throughout the entire range end point is implemented but it is not displayed on the web app due to timing shortage.

Alert Service
Our website also features an alert system, where any visitor can place healthy values as a parameters, as well email and/or password and our server will send an email or SMS message warning the users if our voltages, and current exceed the healthy values.

Every time new data is saved to the database, a new process triggered on a different thread of the OS hosting the server that saved the data. During this after save trigger, the data is compared to all the threshold values provided by different users. If the values of the data that triggered the trigger are below/above the threshold values provided by the user, then the owner of the alert is notified.

Notifications are delivered by email and SMS through the use of Amazon web services infrastructure. To follow the microservices design pattern the email and sms services are completely independent from one another. Both services are hosted in AWS and in order to send an alert, a simple API is provided in which the user only provides the recipients email of phone number as well as the message that is being sent as parameter of a GET HTTP request.

### Cost Analysis

We were given a budget of $1000 dollars, with our grade being dependent on how much we spent. For our turbine, we spent a total of $379 from the budget. This included the following:

- Water-jetting stator and rotor ($137).
- PCBing our designs ($74).
- Buying our electrical components ($167).

However, we were not entirely efficient in our budget and only actually need $229 out of the $379. In regards to the water-jetting, we only used our stator which means that the cost of the rotor waterjet is not justified in our final cost. Our final design required a $72 waterjet. For our components, we spent a lot of money prototyping and doing tests. Although there were lots of components that we haven’t used in our final design, we feel that it was needed for us to forward our ideas the project. A total of $83 of components were crucial out of the $167. In total we only needed to use $229 out of the $379 used, which gives us a budget efficiency of 60%. A full list of exactly what is spent, and what is used is detailed in the appendix.

A lot of the money in our budget was used as prototyping and because of that reason, we can replicate this project for even less. We discovered that we could order PCBs online for $5 + shipping. This would reduce our cost heavily as we’ve expended $74 of our budget on PCBs. With a working final design, we can display the bill of materials of our final design as shown in table 3. The green highlight on the table signifies parts that we’ve already owned before the project. Because we want to be as extensive as possible, we’ve included components that we’ve originally already owned.

Part # | Description | Quantity x Price | Total
M8275-ND | Inductor for Boost Converter | 1 x $3.26 | $3.26
Terminal Blocks | Load, Generator input / output | $0.49 + $0.36 | $0.85
Assorted Resistors | 100k,470k,1M, 100 resistors | N/A | N/A
Assorted Capacitors | 100uF, 200uF | Approx $1. | $1
LM358 | Sensors | 2 x $0.59 | $1.18
22R476C | Schottky Diodes | 7 x $0.39 | $2.73
STP60NF06 (https://www.digikey.com/product-detail/en/stmicroelectronics/STP60NF06/497-2779-5-ND/603804) | N- channel for B.C | 1 x $1.46 | $1.46
MRS-12985L00FE140 | 5mOHM shunt | 1 x $4.96 | $4.96
MIKROE-1530 | Stepper 5V for turbine wind tracking | 1 x $12.15 | $12.15
3382G-1-104G | SMD potentiometer for windtracking + feedback | 2 x $3.96 | $8.00
Arduino Header Pin | .1 in spaced pins | N/A | N/
Magnetic Wire | N/A | N/A | N/a
Arduino Rev 2 | Our mcu | $45 | $45
PCB | For boost converter + SMD potentiometer | $5 x 2 | $10
Waterjet | Stator | $72 | $72
Lego Chassis | | N/A | N/A
Total | N/A | N/A | $162.59
Table3: Final design bill of materials

As shown we can replicate our final design for $162.59. If we discounted all the parts we’ve already owned, then we would have needed $100. That means with our current knowledge, and previously owned parts, we could have replicated this project for $100.

### Timeline

In lieu of the final demonstration and how different our timeline actually was in comparison to our preliminary timeline, we condensed our final Gantt Chart into one single stage. The preliminary Gantt charts have also been included for comparison

Gantt Chart for the project

Figure 25: Final Gantt Chart of the overall project

Preliminary Gantt Charts from our project proposal

Figure 26: Gantt chart for demo 2 of the proposal

Figure 27: Gantt Chart for the final demo in our proposal

Our timeline was more or less met, and our integration process began around 20 days after what we have initially predicted. This is mainly due to a lack of knowledge of when each part could do certain steps (ie. learn how to submit a Waterjet request, PCB submissions). So most of the time was spent waiting until the next steps which will allow us then to integrate.

### Final Remarks

Originally we set out to find out if placing our wind turbines in remote areas were cost efficient. We determined it would cost $162.9 dollars to implement our current design. However, with our current design, our turbine would produce $116/Watt, which makes it uneconomical as well as inefficient. We see that commercial turbines produce about $1.75/Watt, if we were able to scale our project up, maybe we can minimize cost per power. As of now, our design is not feasible. Despite our wind turbine design not being feasible, we did design a monitoring system that can be feasible and implemented on a large scale wind farm. Our website is modular and only requires I2C communication to work. We believe that our website covers the most of the basic functions required to monitor a power system. With that said, we did accomplish our secondary goal, which to learn. We learned a lot during this course, and at the end of this project, we believe that it’s actually more important than our primary goal; with the most important topic learned being I2C communication, HTTP, and PCB design. All in all, we were ecstatic with our final implementation of our wind turbine. Finally, we’d like to formally thank Professor Nacho, Professor Grecu for providing us with this opportunity, and we’d like to thank all the TA’s for all their support during the course.

### References

Sen, Paresh Choudra. Principles of Electric Machines and Power Electronics. Wiley, 1989.

“analogRead()”, Arduino, 19 January 2019, https://www.arduino.cc/reference/en/language/functions/analog-io/analogread/

“Arduino and MCP3008.”, Arduino Learning, 10 Mar 2019 http://arduinolearning.com/code/arduino-and-mcp3008.php

“How wind turbines work”, USDOE, 6 January 2019, ,https://www.energy.gov/eere/wind/how-do-wind-turbines-work’

“MPPT Algorithm”, MathWorks, Feb 16th, 2019, https://www.mathworks.com/discovery/mppt-algorithm.html

“The Differential Amplifier”, Electronics Tutorial, 5 February 2019, https://www.electronics-tutorials.ws/opamp/opamp_5.html

“Unity gain amplifier or voltage follower in a voltage divider”, Analogic Tips, 5 February 2019, https://www.analogictips.com/voltage-follower-unity-gain-amplifier-voltage-divider-faq/

“Wifi Library”, Arduino, 14 February 2019, https://www.arduino.cc/en/Reference/WiFi

### Appendix A : Budget Usage

Components List:

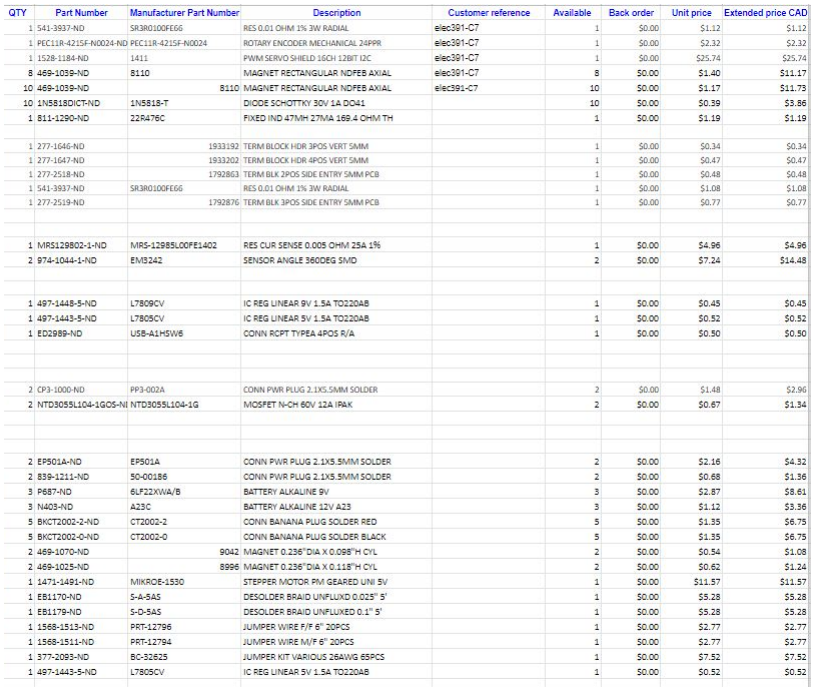
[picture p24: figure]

Waterjet usage : $137
Component : $167
PCB : $74.40

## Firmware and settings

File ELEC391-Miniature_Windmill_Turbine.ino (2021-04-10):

#include <Automaton.h>
#include <AccelStepper.h>
#include <QueueArray.h>

//////////////////// [ INIT GLOBAL CLASSES ] ///////////////////////////////

// Automaton Analog  Interrupt Machine
Atm_analog voltage_meter;
Atm_analog current_meter;
Atm_analog boost_converter;

// Stepper control step,  1, 3,  2, 4
AccelStepper stepper1(8, 11, 7, 10, 8);


//Dynamic Datastructures
QueueArray <int> queue_1;
QueueArray <int> queue_2;

//Automaton timer machines
Atm_timer timer_1;
Atm_timer timer_2;

//////////////////// [ Constant Variables ] /////////////////////////////////

// Wind position controller settings
const int DEFAULT_STEPS    = 90;

// ADC readings scale factors
const float CURRENT_SCALE_FACTOR       = 0.0;
const float BOOST_VOLTAGE_SCALE_FACTOR = 0.0;
const float VOLTAGE_SCALE_FACTOR       = 0.0;

// External Interrupts
const byte INTERRUPT_PIN_1 = 2;
const byte INTERRUPT_PIN_2 = 3;

/////////////////// [ Global variables ] ///////////////////////////////////
/*
 * [ STATES ]
 * 
 * INIT -> 0
 * RUN  -> 1
 * 
 */

float current_voltage       = 0.0;
float current_current       = 0.0;
float current_boost_voltage = 0.0;
float stored_power          = 0.0;
float stored_voltage        = 0.0;
float duty                  = 0.9;
int   interrupt_1_time      = 0;
int   interrupt_2_time      = 0;



void setup() {
  
  //  [ DEBUG ]
  Serial.begin(9600);

  //  [ INIT ]
  // NOTE: Order of initialization important due to dependency injection of machines
  
  //Init External Interrupts
  init_external_interrupts();

  //Init timer interrupts
  init_timer_interrupts();

  // Init voltage meter
  init_voltage_meter();

  // Init current meter
  init_current_meter();

  // Init Voltage Meter Boost Converter
  init_voltage_meter_boost();

  //Init timers
  init_timer_machines();

  // Init stepper
  init_stepper();
}

void loop() {
  // Run automaton machines
  automaton.run();
  // Run stepper
  stepper1.run();
  // Debugging
  //print_readings();
}

/////////////////////// [ EXTERNAL INTERRUPTS ] ///////////////////////////////

/*
 * init_external_interrupts: Initializes external interrupts to read signals from rotor encoder
 *                           to adjust based on wind detector
 *                           -> Uses pin 2,3 (Arduino designated pins for external interrupts)
 */
void init_external_interrupts() {
  Serial.println("External Interrupts Initialized");
  pinMode(INTERRUPT_PIN_1, INPUT_PULLUP);                                                // Set pins to be active on pull-up signal
  pinMode(INTERRUPT_PIN_2, INPUT_PULLUP);                                                // Set pins to be active on pull-up signal
  attachInterrupt(digitalPinToInterrupt(INTERRUPT_PIN_1), interrupt_callback_1, RISING); // Set external interrupt on pin_1. Attach callback <vector>.
  attachInterrupt(digitalPinToInterrupt(INTERRUPT_PIN_2), interrupt_callback_2, RISING); // Set external interrupt on pin_2. Attach callback <vector>.
}

/*
 * interrupt_callback_1: Handles interrupts trigger on interrupt_pin_1.
 *                       -> Gets current time elpsed since progam started in ms
 *                       -> Dicards garbage values and noise by comparing current time elapsed (T) 
 *                          with the last recorded time elapsed (T-1)
 *                       -> Pushes time elapsed to queue_1 and records current elapsed time
 */

void interrupt_callback_1(){
  // Get current time with respecto to counter
  int _time = millis();
  if (_time <= interrupt_1_time + 200) { return; }
  // Push value to queue 
  queue_1.enqueue(_time);
  // Record value
  interrupt_1_time = _time;
  Serial.print("Callback1 ");
  Serial.println(_time);
}

/*
 * interrupt_callback_2: Handles interrupts trigger on interrupt_pin_2.
 *                       -> Gets current time elpsed since progam started in ms
 *                       -> Dicards garbage values and noise by comparing current time elapsed (T) 
 *                          with the last recorded time elapsed (T-1)
 *                       -> Pushes time elapsed to queue_2 and records current elapsed time
 */
void interrupt_callback_2(){
  //Get current time with respecto to counter
  int _time = millis();
  if (_time <= interrupt_2_time + 200) { return; }
  // Push value to queue 
  queue_2.enqueue(_time);
  // Record value
  interrupt_2_time = _time;
  Serial.print("Callback2 ");
  Serial.println(_time);
}

////////////////////////////////// [ TIMER INTERRUPTS ] //////////////////

/*
 * init_timer_interrupts: Timer 1 interrupt set to work at FAST PWM Mode
 *                        -> Frequency and Duty cycle set by wrtting on:
 *                           -> Input Capture Register (Frequency)
 *                           -> Ouput Compare Register (Duty Cycle)
 *                        -> As outlined on Atmega328 datasheet, FAST PWM is set by:
 *                           -> Enabling the COM1A1(R/W), and WGM11(R/W) bits of TCCR1A register
 *                           -> Enabling the CS10(R/W), WGM12(R/W), and WGM13(R/W) bits of TCCR1B register
 */
void init_timer_interrupts() {
  Serial.println("Timer Interrupts Initialized");
  // Set pin to output pwm (Pin 9 is controlled by Arduino's Timer 1)
  pinMode(9, OUTPUT);
  cli();                                        //Stop interrupts (Function located on system's global header file)
  TCCR1A = 0;                                   // Clear TCCR1A
  TCCR1B = 0;                                   // Clear TCCR1B
  TCNT1  = 0;                                   // Initialize counter value to 0
  //Set register bits to enable 16-bit resolution Fast PWM Mode
  TCCR1A = _BV(COM1A1) | _BV(WGM11);
  TCCR1B = _BV(CS10) | _BV(WGM12) | _BV(WGM13);

  ICR1 = 1000;                                  // Input Capture Register set to 1000. Frequency approx 15,500,000/1000 = 15.5kHz
  OCR1A = duty*1000;                            // Output Compare Register set to a ratio of pwm signal length (0.00<->1.00)*ICR1 = Duty Cycle
  sei();                                        //Allow interrupts (Function located on system's global header file)
}

/////////////////////// [ VOLTAGE METER ] //////////////////////

/*
 * init_voltage_meter: Initializes Automaton analog state machine for voltage readings
 */
 void init_voltage_meter() {
      Serial.println("Voltage Meter Initialized");
      voltage_meter.begin(A1, 50) //For now analog read is polled every 50 ms
      .onChange(voltage_callback, 3);
      //TODO: Calibrate poll rate to optimal rate after integarting all hardware components
 }

 /*
 * voltage_callback: Callback triggered every time wind_detector sense changes in its analog read.
 * 
 * params: idx - Index of callback being triggered
 *         v   - Updated value of wind_detector read
 *         up  - Flag indicating if updated values is greater [ 1 ] or less than old [ 0 ] value
 * TODO: Calculate conversion factor for ADC readings when integrated with hardware
 */
void voltage_callback( int idx, int v, int up ) {
    current_voltage = (float) v;
}
 
/////////////////////// [ CURRENT METER ] ///////////////////////////////

/*
 * init_current_meter
 */
void init_current_meter() {
  Serial.println("Current Meter Initialized");
  current_meter.begin(A2, 50)
  .onChange(current_callback, 3);
}

/*
 * current_callback: Callback triggered every time wind_detector sense changes in its analog read.
 * 
 * params: idx - Index of callback being triggered
 *         v   - Updated value of wind_detector read
 *         up  - Flag indicating if updated values is greater [ 1 ] or less than old [ 0 ] value
 * TODO: Calculate conversion factor for ADC readings when integrated with hardware
 */
void current_callback( int idx, int v, int up ) {
  current_current = (float) v;
}

/////////////////////// [ BOOST VOLTAGE METER ] //////////////////////

/*
 * init_voltage_meter_boost: Initializes Automaton analog state machine for voltage readings after boost converter
 */
 void init_voltage_meter_boost() {
      Serial.println("Voltage Meter (Boost) Initialized");
      boost_converter.begin(A3, 50)
      .onChange(boost_callback, 3);
 }

 /*
 * boost_callback: Callback triggered every time wind_detector sense changes in its analog read.
 * 
 * params: idx - Index of callback being triggered
 *         v   - Updated value of wind_detector read
 *         up  - Flag indicating if updated values is greater [ 1 ] or less than old [ 0 ] value
 * TODO: Calculate conversion factor for ADC readings when integrated with hardware
 */
void boost_callback( int idx, int v, int up ) {
    current_boost_voltage = (float) v;
}

/////////////////////// [ TIMER MACHINES ] //////////////////////

/*
 * init_timer_machines: Initializes Automaton timer machines
 */

void init_timer_machines() {
    timer_1.begin( 0.5 )          // Set timer interval to 0.5 miliseconds
    .repeat( -1 )                 // Set timer to repeat indefinitively
    .onTimer( timer_1_callback )  // Attach timer trigger to callback
    .start();
    timer_2.begin( 1 )            // Set timer interval to to 1 milisecond
    .repeat( -1 )                 // Set timer to repeat indefinitively
    .onTimer( timer_2_callback )  // Attach timer trigger to callback
    .start();
    Serial.println("Timer Machines Initialized");
}

/*
 * timer_1_callback: Handles timer triggers. Continously check for the size of the
 *                   interrupt queues and adjust stepper position accordingly
 *                   -> Checks if the queues containing external interrupts elapsed 
 *                      time are empty or unequal. If so < return >
 *                   -> Checks if stepper motor is currently being adjusted if so < return >
 *                   -> Pops the oldest values of both queues (FIFO)
 *                   -> Compares times elapsed to adjust stepper motor on proper direction
 */
void timer_1_callback( int idx, int v, int up ) {

  if(queue_1.isEmpty() || queue_2.isEmpty()) { return; } // Check if empty
  if(queue_1.count() != queue_2.count()) { return; }     // Check equeal lengths 
  if(stepper1.distanceToGo() != 0) { return; }           // Checks if stepper is being used
 
  int val_1 = queue_1.dequeue();                         // Pop data out of queue
  int val_2 = queue_2.dequeue();                         // Pop data out of queue
  if(val_1 < val_2) {
    //Move stepper 15 degrees right
      turn_right();
  }
  else if(val_1 > val_2) {
    //Move stepper 15 degress left
      turn_left();
  }
  Serial.print("Val1:");
  Serial.println(val_1);
  Serial.print("Val2:");
  Serial.println(val_2);
}

/*
 * timer_2_callback: Handles timer tiggers. Calls MPPT algorithm when called.
 */
void timer_2_callback( int idx, int v, int up ) {
  track_max_power();
  return;
}

////////////////////////////////// [ STEPPER ] //////////////////////////

/*
 * init_stepper: Initializes stepper class
 */
void init_stepper() {
  // Set stepper max speed
  stepper1.setMaxSpeed(1000.0);
  // Set stepper accelaration (1000, is fastest)
  stepper1.setAcceleration(1000.0);
  // Set stepper speed (For some reason there is no much difference between values)
  // TODO: Investigate MaxSpeed, Acceleration and Speed for stepper motor used on final demo
  stepper1.setSpeed(1000);
}


/*
 * turn_right_by: Turns stepper right by 'N' steps
 * 
 * params: steps - Number of steps to move right
 */
void turn_right_by(int steps) {
  Serial.print("Move right by: ");
  Serial.println(steps);
  stepper1.moveTo(stepper1.currentPosition() + steps);
}

/*
 * turn_left_by: Turns stepper left by 'N' steps
 * 
 * params: steps - Number of steps to move left
 */
void turn_left_by(int steps) {
  Serial.print("Move left by: ");
  Serial.println(steps);
  stepper1.moveTo(stepper1.currentPosition() - steps);
}

/*
 * turn_right: Turns stepper right by default steps
 */
void turn_right() {
  Serial.print("Move right by: ");
  Serial.println(DEFAULT_STEPS);
  stepper1.moveTo(stepper1.currentPosition() + DEFAULT_STEPS);
}

/*
 * turn_left: Turns stepper left by default steps
 */
void turn_left() {
  Serial.print("Move left by: ");
  Serial.println(DEFAULT_STEPS);
  stepper1.moveTo(stepper1.currentPosition() - DEFAULT_STEPS);
}

////////////////////////////////// [ MPPT ] /////////////////////////////

/*
 * track_max_power: Entry point to MPPT Algorithm
 */

void track_max_power() {
  float voltage = current_voltage;             // Get current Voltage Reading
  float current = current_current;             // Get current Current Value
  float current_power = voltage*current;       // Compute current Power
  // Check if current power is greater than previously stored power
  if( current_power > stored_power ) {
    compare_voltages(voltage, true);           // Handle scenario in which current poer is greater than stored value
  }
  else {
    compare_voltages(voltage, false);          // Handle scenario in which current power is less than sotred value
  }
  store_power_voltage(voltage, current_power); // Store current power and voltage 
}

/*
 * compare_voltages : Handles difference between current voltage and stored voltage
 *                    -> Adjust Duty Cycle according to MPPT Algorithm
 */

void compare_voltages(float voltage, bool is_current_power_greater) {
  if(voltage > stored_voltage && is_current_power_greater) {
    //Increase Duty cycle
    increase_duty_cycle();
  }
  else if(voltage > stored_voltage && !is_current_power_greater) {
    // Decrease Duty cycle
    decrease_duty_cycle();
  }
  else if(voltage < stored_voltage && is_current_power_greater) {
    //Decrease Duty cycle
     decrease_duty_cycle();
  }
  else if(voltage < stored_voltage && !is_current_power_greater) {
    //Increase Duty cycle
    increase_duty_cycle();
  }
}

/*
 * store_power_voltage: Stores power and voltage in global variables
 */
void store_power_voltage(float voltage, float power) {
  stored_power   = power;
  stored_voltage = voltage;
}

/*
 * increase_duty_cycle: Increases duty cycle by 0.01 units of magnitude
 *                      -> Adds 0.01 units to Duty Cycle mutiplier
 *                      -> New Output Compare Register value is computed and written on ICR1 register
 *                         -> The new value of hardware register ICR1, will produce an increment of duty cycle
 */
void increase_duty_cycle() {
  duty = duty + 0.01;
  OCR1A = duty*100;
}

/*
 * increase_duty_cycle: Increases duty cycle by 0.01 units of magnitude
 *                      -> Adds 0.01 units to Duty Cycle mutiplier
 *                      -> New Output Compare Register value is computed and written on ICR1 register
 *                         -> The new value of hardware register ICR1, will produce an decrement of duty cycle
 */
void decrease_duty_cycle() {
  duty = duty - 0.01;
  OCR1A = duty*100;
}

///////////////////////// [ Log Handlers ] ////////////
void print_readings() {
  Serial.print("Voltage: ");
  Serial.print(current_voltage);
  Serial.print("    Current: ");
  Serial.print(current_current);
  Serial.print("    Boost Voltage: ");
  Serial.println(current_boost_voltage);
}
